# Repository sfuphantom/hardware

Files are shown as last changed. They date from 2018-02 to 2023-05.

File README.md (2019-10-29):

# hardware
Schematics and layout work 

## Getting started with git

Tutorial: https://www.youtube.com/watch?v=1xfp2Cx9FUk

the main workflow is usually like this:

1. install git on your machine https://git-scm.com/download/
2. use the git bash terminal window to work with the repositories:
3. clone the repository of choice: in your terminal window, navigate to the folder you want to store the repository in, and send the command `git clone` https://github.com/sfuphantom/hardware.git' for the hardware repository for example
4. the hardware repo has folders that contain a submodule - which is essentially just a version of a different repo, nested inside the hardware folder. this nested repo is the altium-libraries repository! to enable it, use `git submodule init` while in the hardware directory, and then `git submodule update`
5. now if you navigate to that folder in your normal file browser, you should see the repository folder with all the files in it
6. you can now edit the files and add new files into the repository folder like normal, as you would any folder system
7. to register new added files you have placed in the repository folder in your file browser, use the command `git add -A` in your terminal window while in the directory of your repository (`cd /documents/phantom` will change your active directory to /documents/phantom, and `cd ..` will change your active directory up one level)
8. Make sure you create a new branch before editing any files! Branching instructions down below
9. Once in your new branch, `git add -A` will add all new files repo folder to be tracked by git
10. to save the changes you have made and the files you have added, use the command `git commit -m "fill in your update here"` to commit your changes and save them with a useful message
11. when you are ready to update the centralized repository on github with your changed localized cloned repository, use the command `git push` and you should see your changes show up on github

http://rogerdudler.github.io/git-guide/

https://learngitbranching.js.org/

http://www.ndpsoftware.com/git-cheatsheet.html#loc=workspace

## Branching

If you wish to work on a version of the repo without affecting or potentially causing conflicts, use **branches**. They are very useful for developing a new feature of a program/board without affecting the master branch. They can later be merged into the master branch by using a **pull request**. 
1. Navigate to your hardware directory in the git bash terminal window.
2. Use the following command `git branch MyBranchName` to create a new branch
3. Use the following command `git checkout MyBranchName` to switch your active branch to MyBranchName instead of Master
4. If you want to perform both commands in one line, here's a shortcut: `git checkout -b MyBranchName`
5. Now you can develop and make changes as you wish on MyBranchName, adding files, making commits, and pushing up to the repository held in Github. 
6. When you have decided you are ready to combine your changes/additions to the master branch of the repository, use Github's web interface (https://github.com/sfuphantom/hardware) to create a **new pull request**.
7. A pull request will alert other people that you are ready to combine your branch (MyBranchName) with the Master branch, and will allow them to review your work and approve it for merging.

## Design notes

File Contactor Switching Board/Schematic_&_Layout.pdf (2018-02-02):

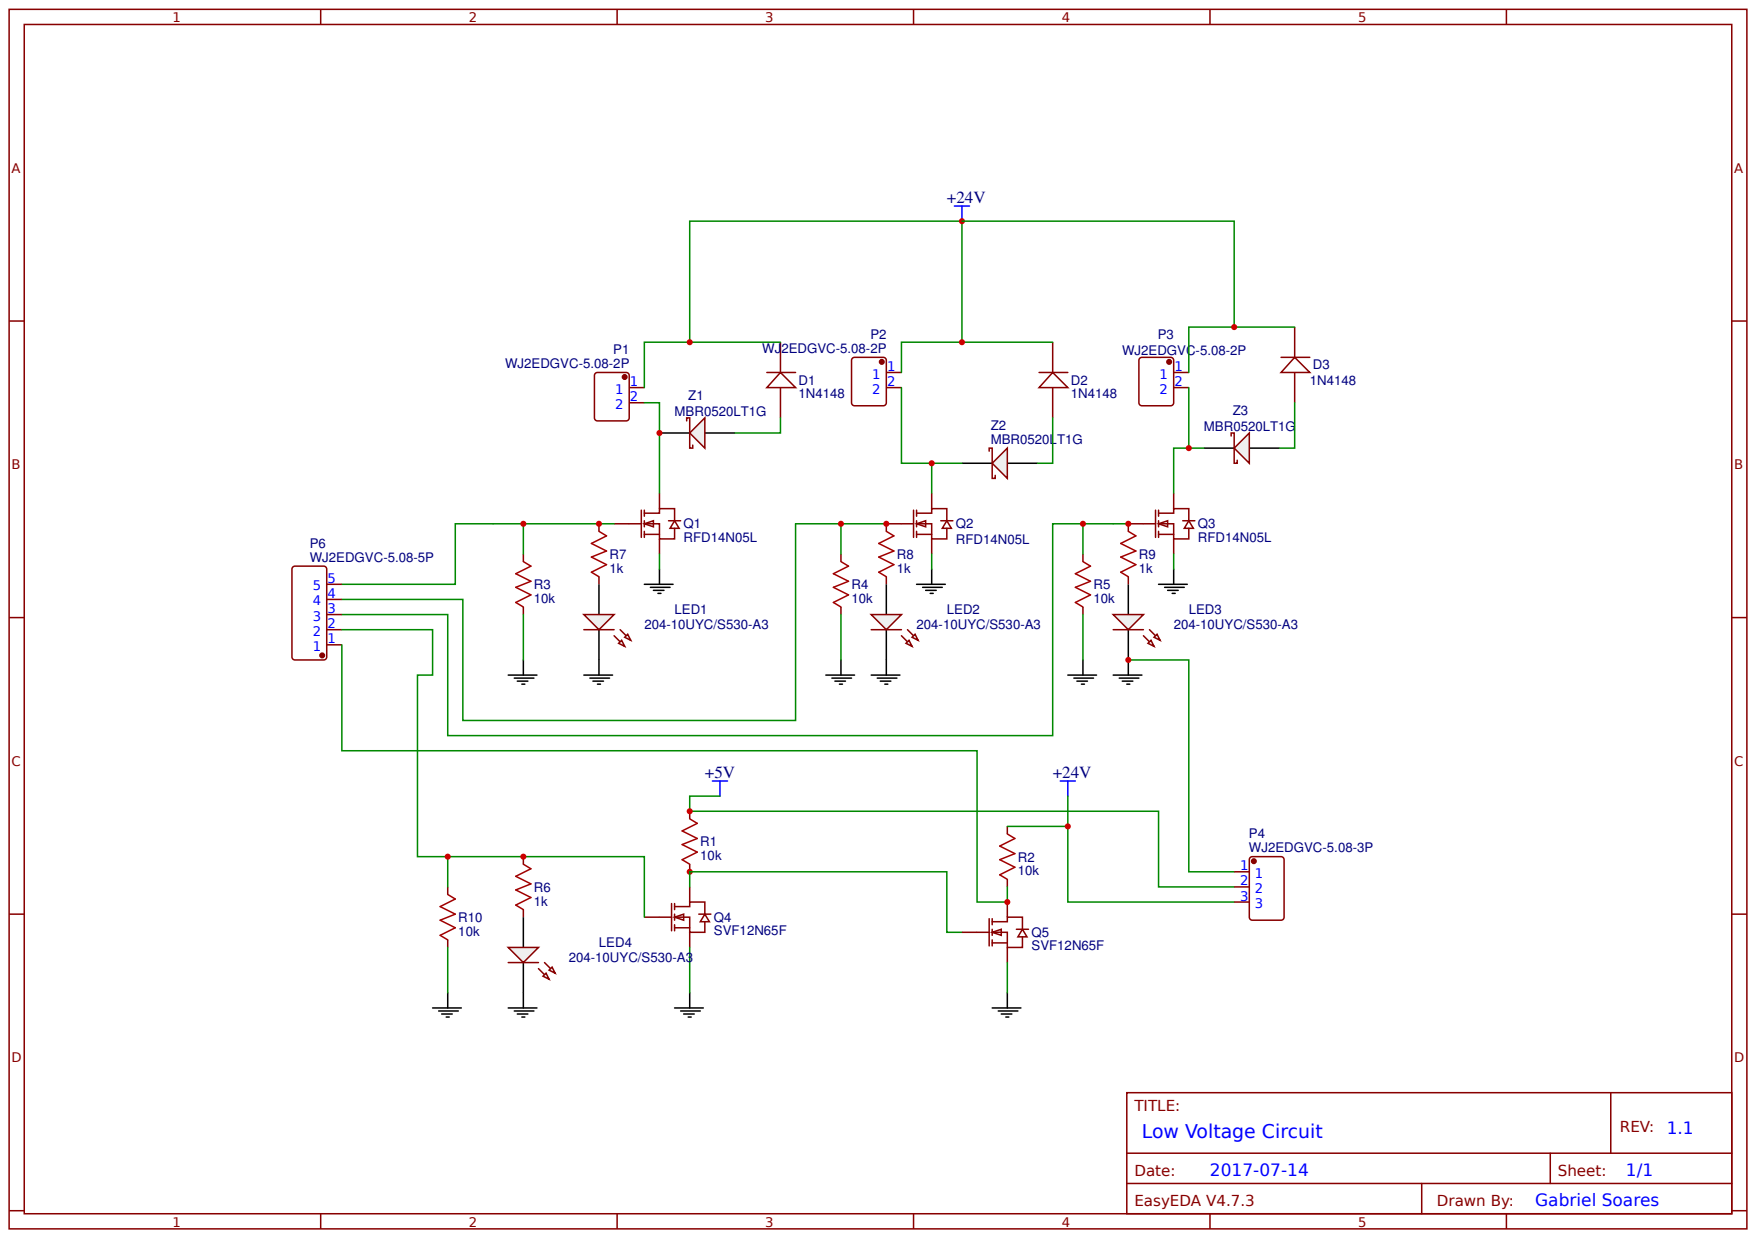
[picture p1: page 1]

Powered by TCPDF (www.tcpdf.org)Powered by TCPDF (www.tcpdf.org)

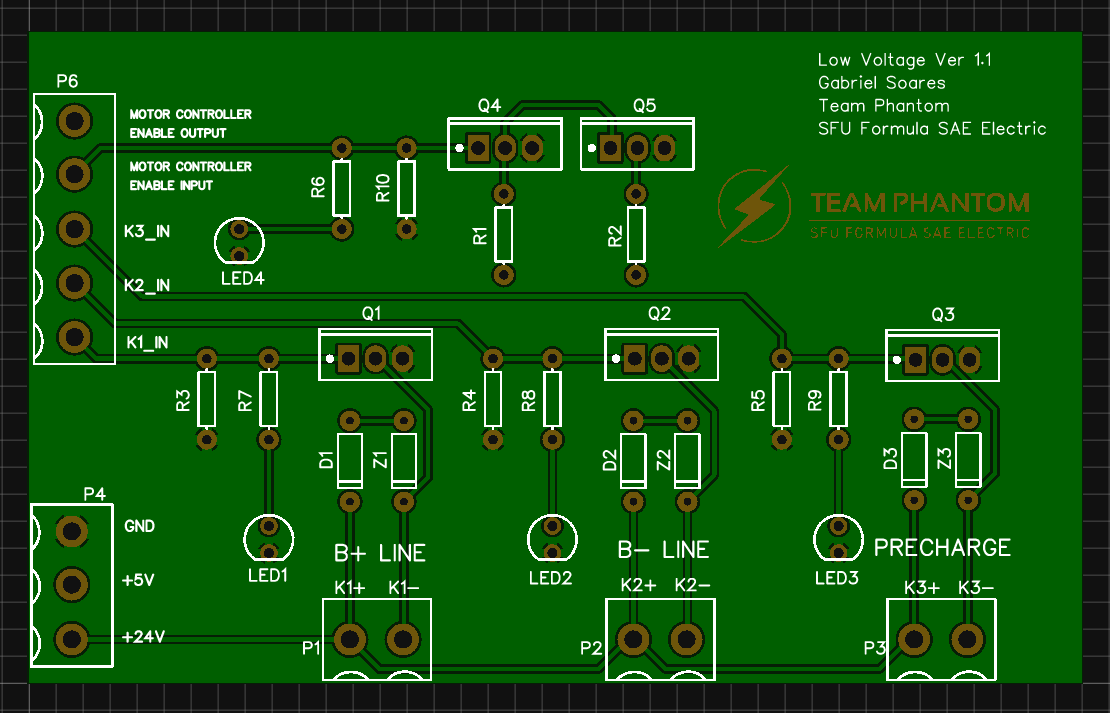
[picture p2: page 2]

Powered by TCPDF (www.tcpdf.org) Powered by TCPDF (www.tcpdf.org) Powered by TCPDF (www.tcpdf.org) Powered by TCPDF (www.tcpdf.org)

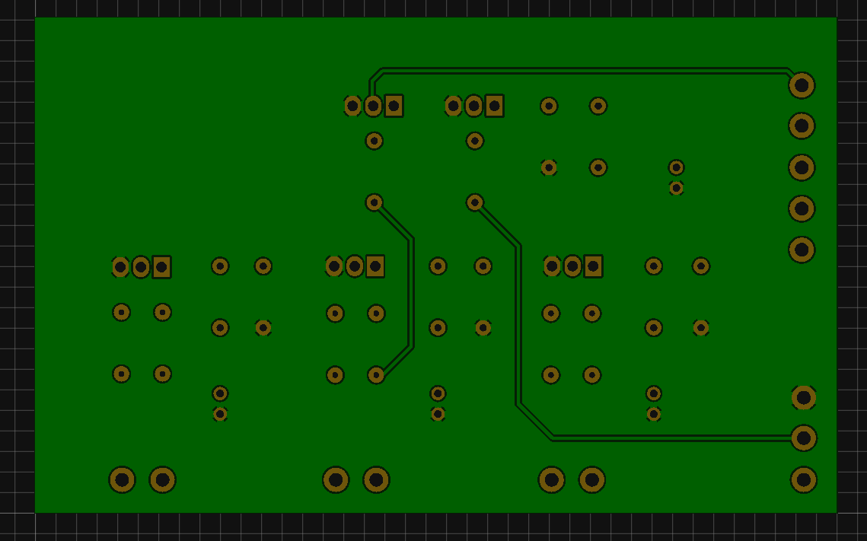
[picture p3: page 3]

Powered by TCPDF (www.tcpdf.org) Powered by TCPDF (www.tcpdf.org)

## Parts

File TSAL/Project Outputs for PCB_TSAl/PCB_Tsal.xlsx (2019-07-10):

Comment | Description | Designator | Footprint | LibRef | Quantity
Fuse |  | F1 | FUSE_SMD | 0678D0800-02 | 1
HV |  | J1 | 2_PIN_CONNECTOR | 0705530001 | 1
LV |  | J2 | 2_PIN_CONNECTOR | 0705530001 | 1
RED LED |  | J3 | 2_PIN_CONNECTOR | 0705530001 | 1
GREEN LED |  | J4 | 2_PIN_CONNECTOR | 0705530001 | 1
NTD2955T4G | Trans MOSFET P-CH 60V 12A 3-Pin(2+Tab) DPAK T/R | Q1 | DPAK228P991X238-3N | NTD2955T4G | 1
IPD50N06S4L-12 | MOSFET N-CH 60V 50A TO252-3-11 | Q2 | DPAK228P998X235-3N | IPD50N06S4L-12 | 1
33k Ohm | RES SMD 33K OHM 5% 1W 2512 | R1 | RESC6332X07N | RMCF2512JT33K0 | 1
1K OHm | RES 1K OHM 1% 1/4W 0805 | R2 | RESC2012X06N | RNCP0805FTD1K00 | 1
190Ohm |  | R3 | RESC2012X06N | RC0805FR-0719R1L | 1
560 Ohm | RES SMD 560 OHM 5% 0.4W 0805 | R4 | RESC2012X06N | ESR10EZPJ561 | 1
EL3H7(B)(TA)-VG | OPTOISOLATOR 3.75KV TRANS 4-SSOP | U1 | SOIC127P700X200-4N | EL3H7(B)(TA)-VG | 1

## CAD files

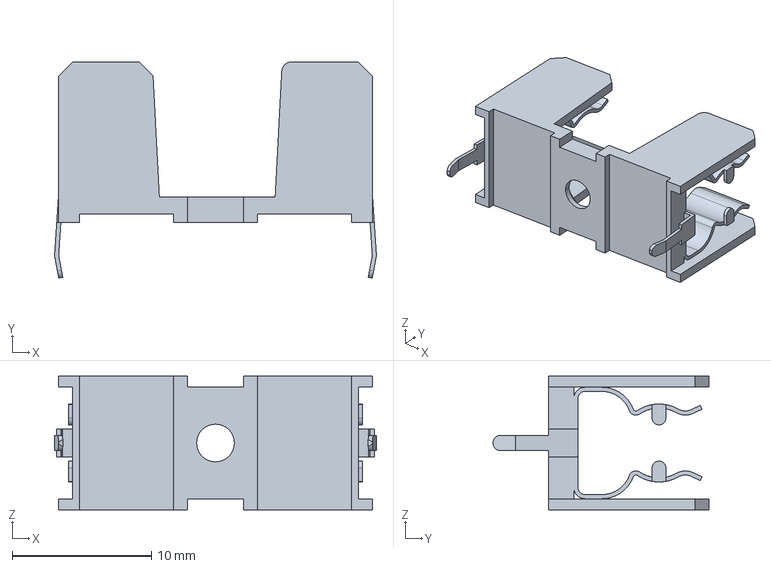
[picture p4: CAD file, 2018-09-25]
PDB/step_files/fuse.stp
23.1 x 15.5 x 9.60 mm

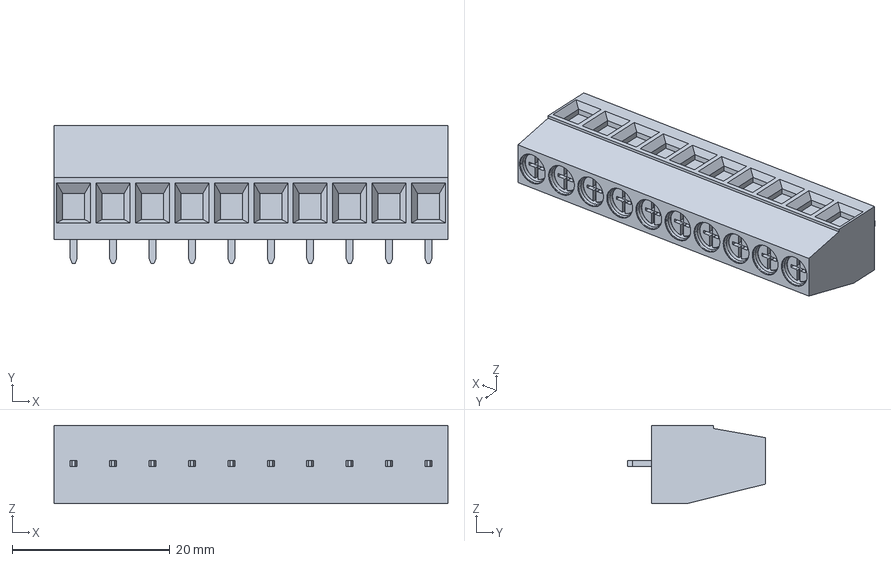
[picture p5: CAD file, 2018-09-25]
PDB/step_files/hdr2.stp
50.0 x 17.5 x 9.91 mm

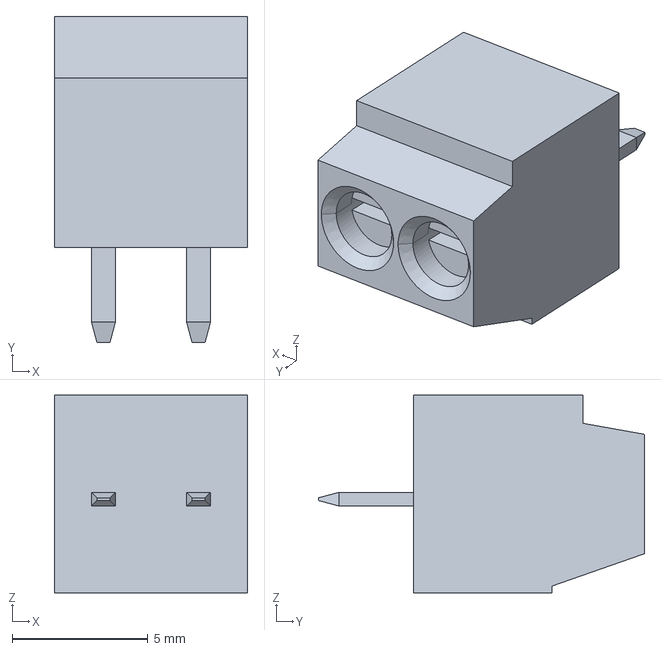
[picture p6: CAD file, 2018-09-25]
PDB/step_files/hdr1.stp
7.11 x 12.0 x 7.29 mm

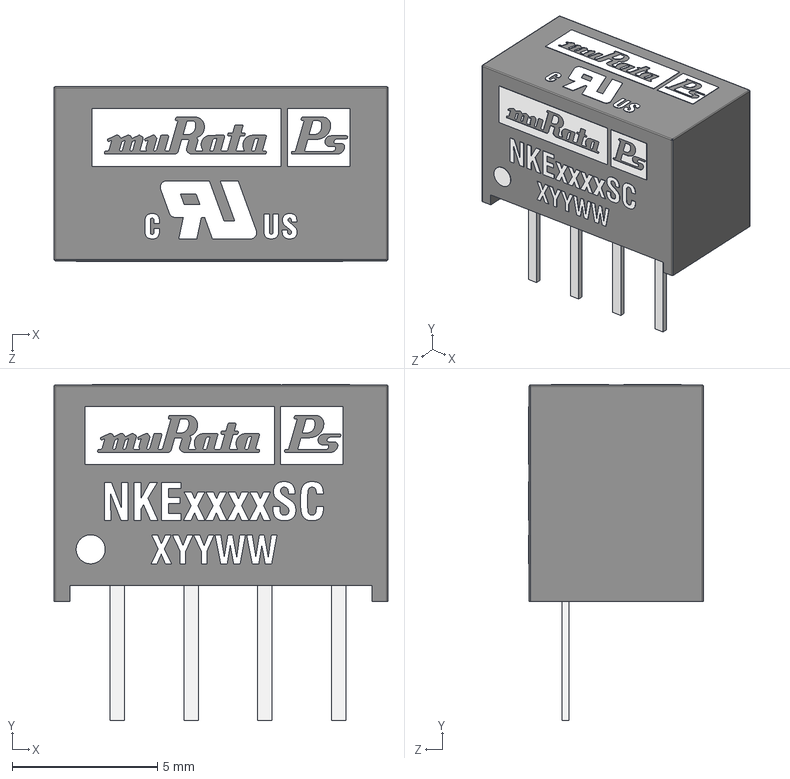
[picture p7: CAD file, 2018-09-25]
PDB/step_files/dcdc2.step
11.5 x 11.6 x 6.02 mm

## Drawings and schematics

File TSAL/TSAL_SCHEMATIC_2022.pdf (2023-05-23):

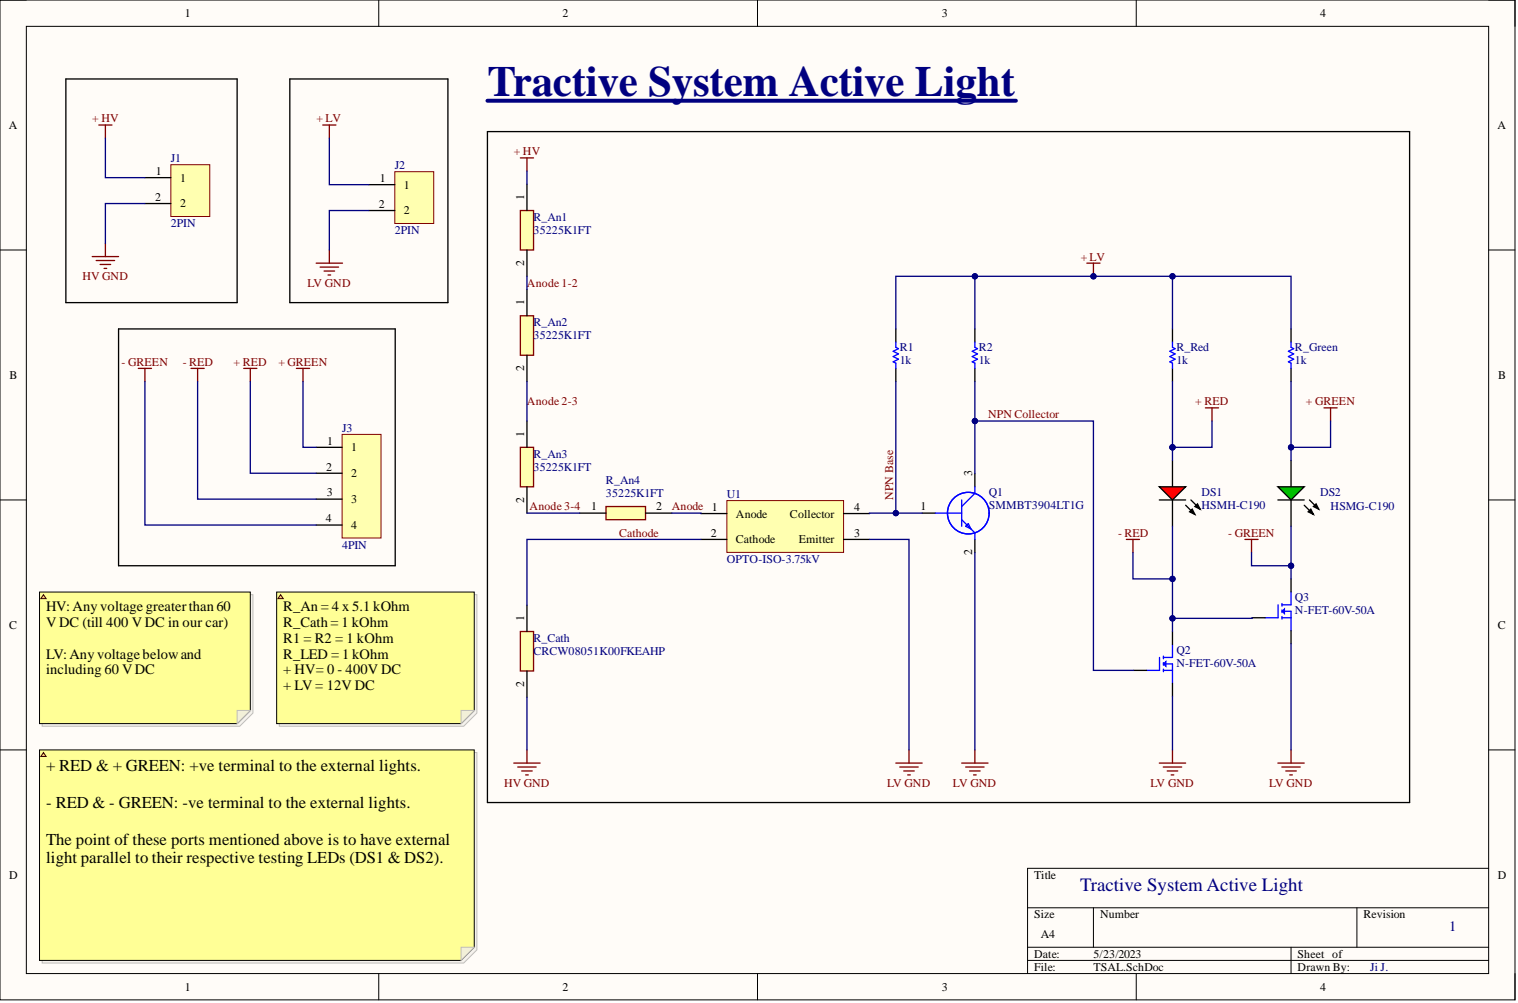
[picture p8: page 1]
1 2 R_Cat; NPN Base; NPN Co; ater th; V DC (till; + RED; the external; - RED; these ports; ioned above; ight paral; their respect; ing LEDs (DS1

Tractive System Active Light

The point of

to have external

Tractive System Active Lig

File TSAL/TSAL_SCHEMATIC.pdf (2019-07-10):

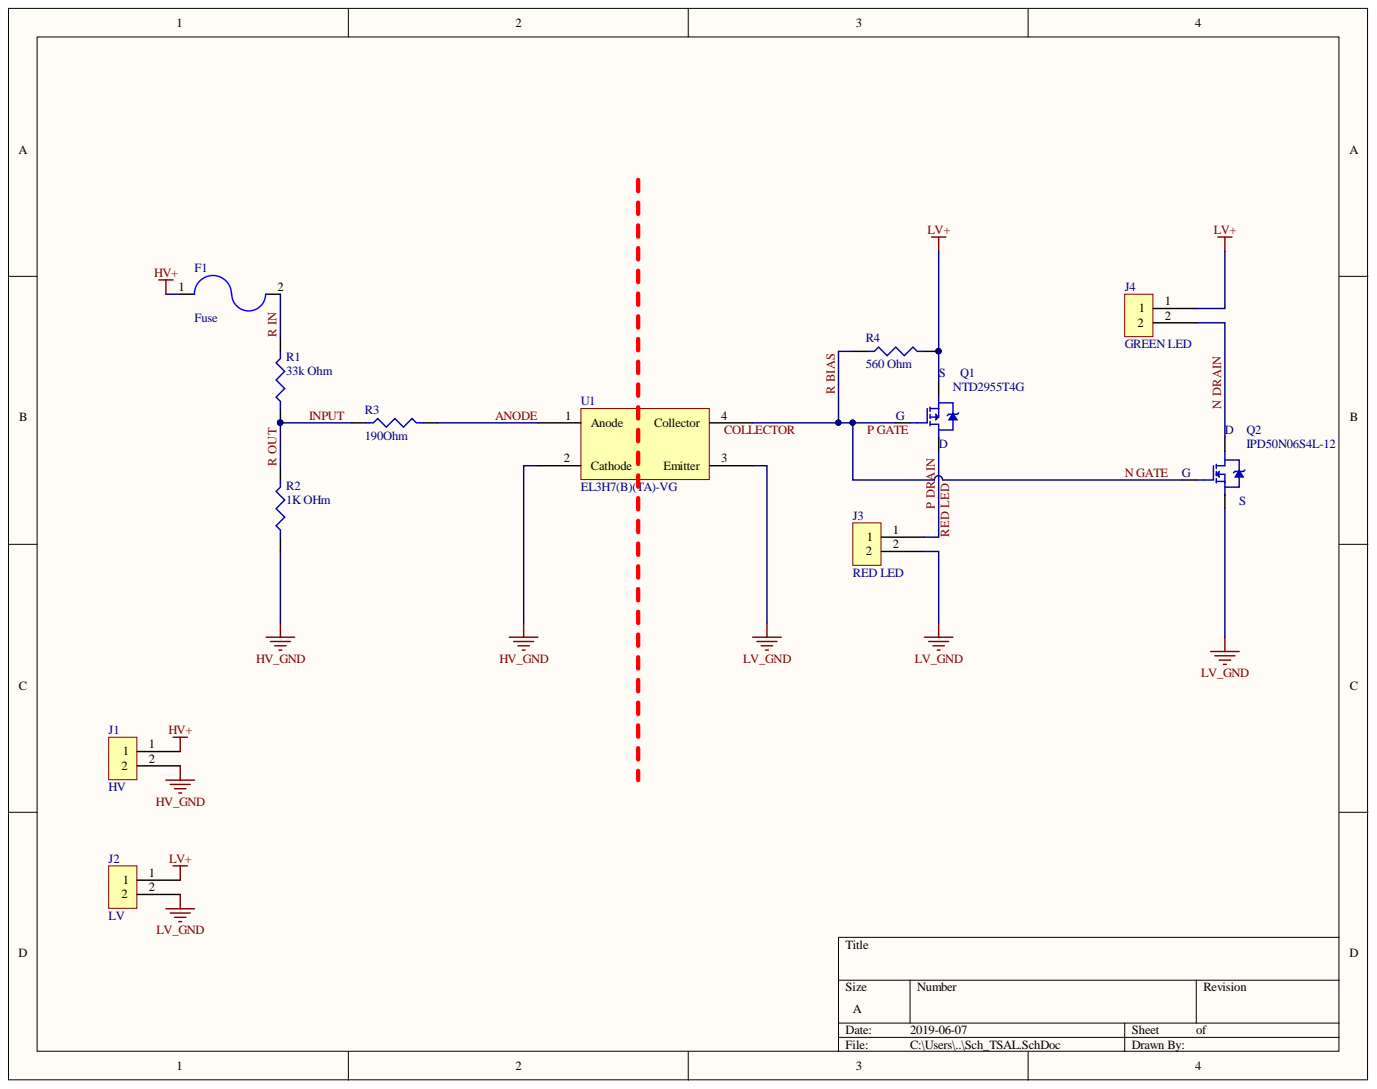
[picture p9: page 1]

Anode 1

COLLECTOR

Size A | Number | Revision

Date: 2019-06-07 | Sheet of
File: C:\Users\..\Sch_TSAL.SchDoc | Drawn By:

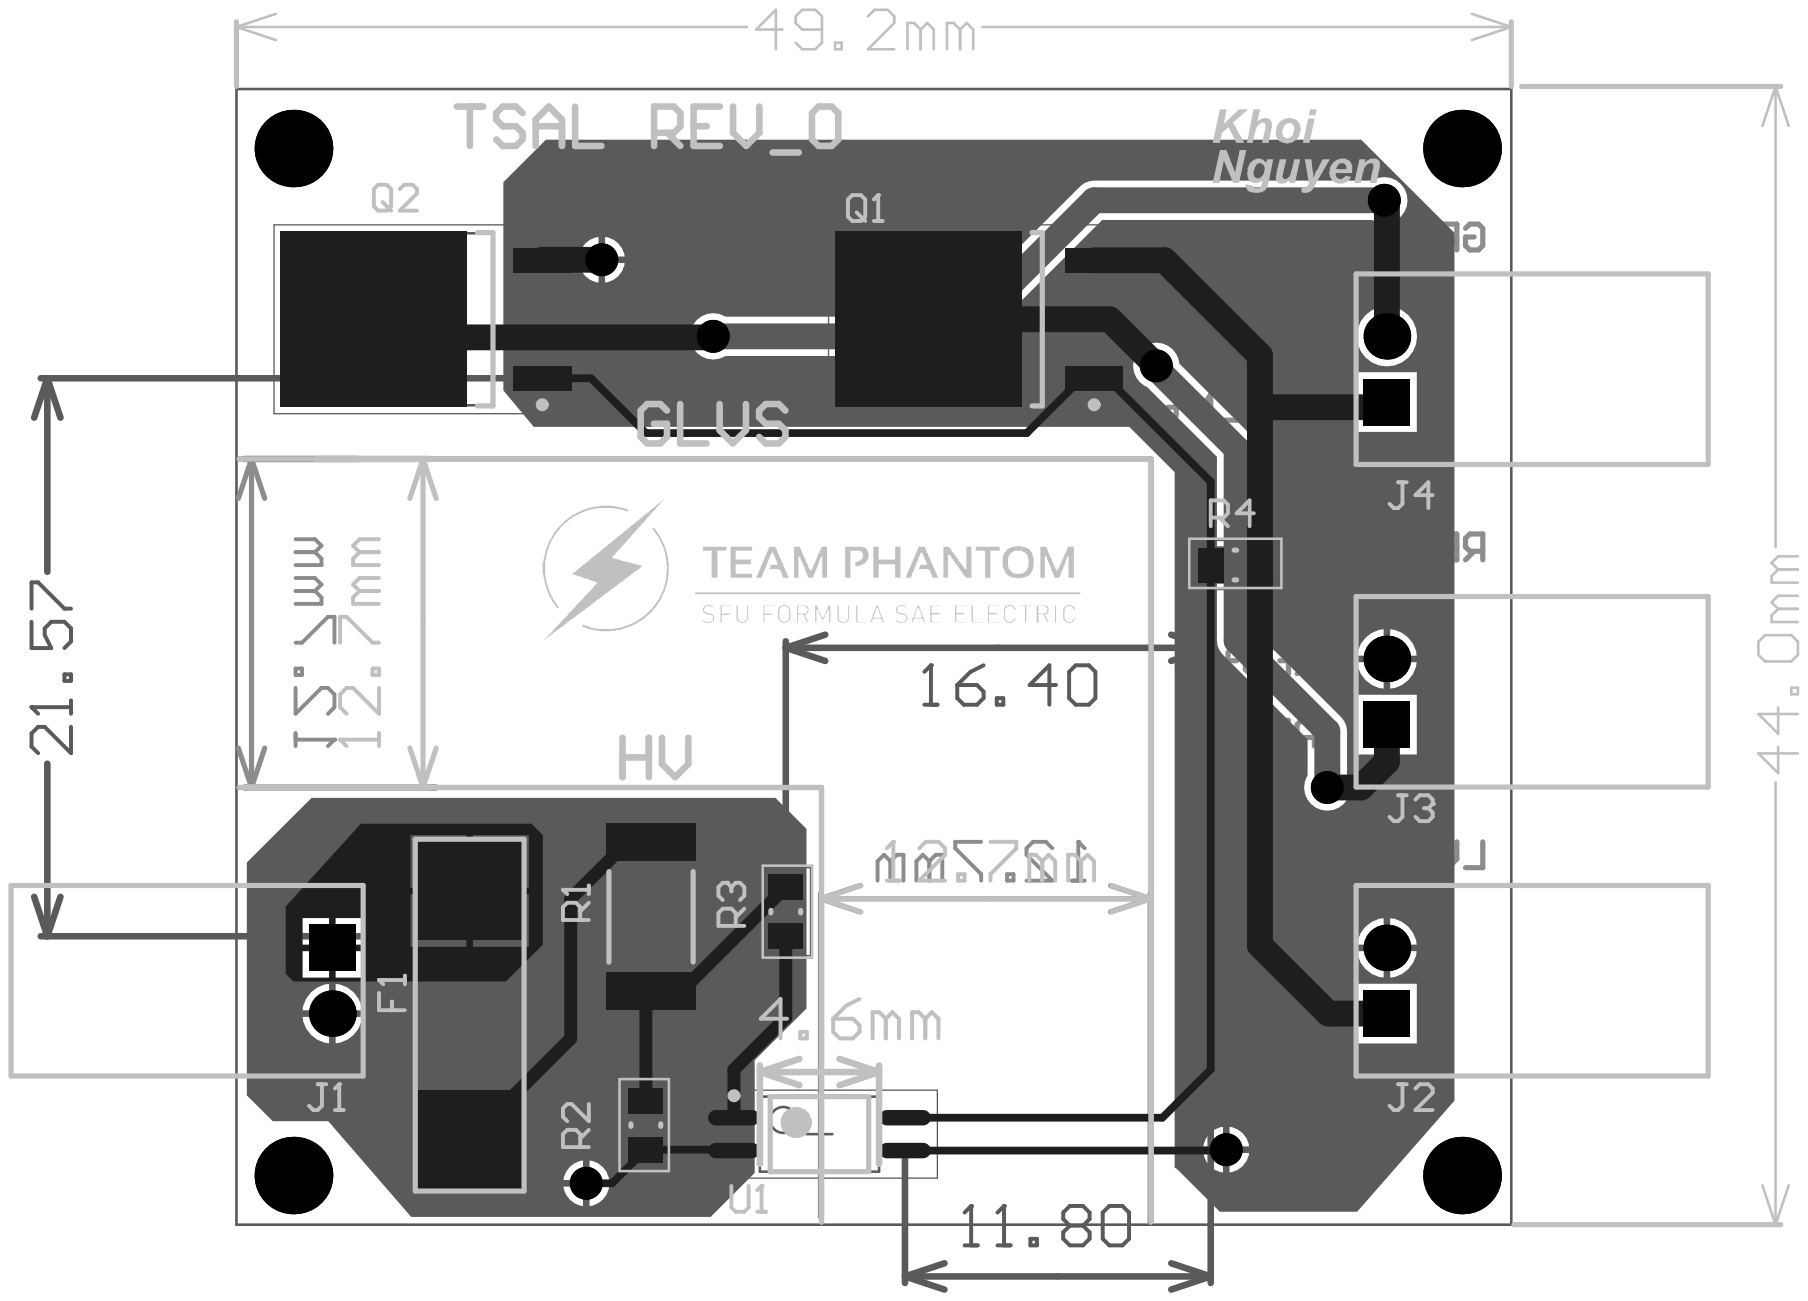
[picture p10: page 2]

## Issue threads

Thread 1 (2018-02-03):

24V Input Connector

gabesoares, 2018-02-03:
Need to find 24V input connector for power input to VCU

gabesoares, 2018-02-07:
Will use Molex MegaFit Connectors:
https://www.molex.com/molex/products/family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

Up to 23.0A current capability
12 - 16 AWG

Board Connector: https://www.digikey.com/products/en?keywords=0768250002

Wire Crimp Connector: https://www.digikey.com/products/en?keywords=1700010102

Crimp Sockets: 12 AWG - https://www.digikey.com/product-detail/en/molex-llc/0768230322/WM11982CT-ND/5639626
14 & 16 AWG - https://www.digikey.com/product-detail/en/molex-llc/0768230321/WM11981CT-ND/5639625

Closed 2018-02-07.

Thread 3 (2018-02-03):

Error Reset Push Buttons

gabesoares, 2018-02-03:
Add push buttons for nPORRST and nRST as inputs to the TMS570 mcu

gabesoares, 2018-02-08:
Added, soft reset and hard reset

Closed 2018-02-08.

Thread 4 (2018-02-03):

Higher Current DCDC

gabesoares, 2018-02-03:
Should we replace the 2A 24->5V DCDC with a higher current one?  Additional current draw from new components plus inrush on the AIRs will likely exceed the rating of our current DCDC, which would result in the voltage rail dropping

gabesoares, 2018-03-19:
Yes

Closed 2018-03-19.

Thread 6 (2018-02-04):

Prototype Latching Circuit

gabesoares, 2018-02-04:
Order components and prototype JK flip flop latching circuit
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

gabesoares, 2018-02-04:
Desired operation: fault signal is sending 0 as all is good, then a fault occurs and the signal sends a 1 (+5V) for a second and then drops back to 0.. We want this 1 to stay latched forever...

JK Flip Flop Logic:
If J=0, K=0, then output Q (& Q bar) stays latched to whatever it was before
If J=1, K=0, then output Q is set to 1, and Q bar is set to 0
If J=0, K=1, then output Q is set to 0, and Q bar is set to 1
If J=1, K=1, then output Q and Qbar are both toggled to the opposite of what they were before

NOTE: A clock signal is needed for the JK flip flop, a 555 timer can be used to generate the clock, but the exact circuit will need to be looked up

The push button attached to the K input will allow the output Q to be reset to 0, and Q bar to be reset to 1.
The red error LED should light up if the fault signal sends a 1 and the output is latched, and turn off when the push button (reset) attached to the K input is pressed.

The green LED should be on in normal operation, and as soon as the fault signal sends a 1. It should stay off until the reset push button is pressed. (This green LED simulates the relay coils of the AIRs)

gabesoares, 2018-02-08:
Prototype this latching circuit as well, talk to Will to learn more about it:

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

Will-McKnight-604, 2018-02-14:
Updated Latching Circuit

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

gabesoares, 2018-02-14:
Latest latching circuit
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

gabesoares, 2018-02-14:
Will need high side driver instead of FET, since vgs will be tough to get without a charge pump, especially with a microcontroller output:

This one looks good, Rds(ON) a little high but not really significant for low current and turning on a relay, it also has a lower pin count and less external components than the other automotive TI ones
http://www.ti.com/product/tps1h000-q1

Will-McKnight-604, 2018-02-20:
Hanieh is taking the flip-flop circuit and prototyping that one, I'll be doing the latest latching circuit

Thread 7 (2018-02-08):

Prototype Shutdown Circuit

gabesoares, 2018-02-08:
Prototype first version of shutdown circuit. Wire inline buttons to simulate the inertia switch, brake over travel switch, HVD, and other master switches.

Use mosfets as shown in attached picture, you might need to be careful about the Vgs of each fet.
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

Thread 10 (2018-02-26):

Find better 1V2 zener diode

gabesoares, 2018-02-26:
3.3V reverse breakdown might be too high.. will likely need new footprint

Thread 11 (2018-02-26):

Change via sizes to bigger holes

gabesoares, 2018-02-26:
Current holes result in min hole size being changed to 0.2 from fab house

gabesoares, 2018-06-09:
Changing from 0.4mm to 0.6mm seems to work

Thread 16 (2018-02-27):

Find smaller crystal

gabesoares, 2018-02-27:
Current one too big, good price though ($0.46 usd)

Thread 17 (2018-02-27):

Find new MCU

gabesoares, 2018-02-27:
Stay within tms570 family, find one with smaller packaging since we don't use all the pins anyway, and one that can be sampled from TI

gabesoares, 2018-10-24:
Figure out how different the TMS570LS1227PGEQ1 is from our TMS570LS1224PGEQ1.... since this one we can potentially sample from TI. Might be worth a few changes to switch to this one. Looks like most of the same features are there, need to verify pinout.
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

gabesoares, 2018-10-30:
Almost identical, but x1227 has FlexRay in addition so has a few less GPIOs than the x1224. Other than these the pinout is identical. Managed to get 3 ICs sampled which is good. Need to be careful tho cause if can't get more sampled, they cost $37 each from Digikey...

http://www.ti.com/lit/ds/symlink/tms570ls1227.pdf

gabesoares, 2019-04-18:
Done, validated TMS570LS1227 on REV1 of VCU

Closed 2019-04-18.

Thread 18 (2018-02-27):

Change routing from D15

gabesoares, 2018-02-27:
Trace on ground side of zener should be on bottom layer

gabesoares, 2018-12-30:
Fixed in vcu-hw rev1

Closed 2018-12-30.

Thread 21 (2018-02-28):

Add voltage sensing on all the rails

gabesoares, 2018-02-28:
Using op amps to compare voltage rails to ensure they are operating nominally. Currently even if a rail is half up (i.e. 24V rail is running at 12V for some reason), our power good LED will still turn on

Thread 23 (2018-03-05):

Create footprint for combined conector

gabesoares, 2018-03-05:
The two molex stac64 connectors need a combined footprint with the mounting holes 4.96mm apart, with both 3d models in one part.

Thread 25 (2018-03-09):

Switch to cheaper FETs

gabesoares, 2018-03-09:
Use lower rated FETs on VCU, current ones are overkill and can handle way too much (i.e. 110 amps). They are expensive, too big, and also hard to solder

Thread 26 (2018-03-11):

Add pull down resistors to ADC input

gabesoares, 2018-03-11:
Without pulldowns they will float, i.e. if a wire disconnects by accident the signal won't be zero

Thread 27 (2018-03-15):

Add EEPROM for parameter saving

gabesoares, 2018-03-15:
Add EEPROM IC to VCU, is useful to dump parameters and values periodically in case of an unexpected loss of power. Upon reset of MCU data can be loaded back with a timestamp of the last data dump

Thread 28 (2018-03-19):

Higher Current DCDCs

gabesoares, 2018-03-19:
Find higher current DCDCs for 3V3 and 5V rails, current ones blow really easily (5V one at 2A and 3V3 one at 300mA). Also find ones that have a much smaller footprint to save board space

gabesoares, 2019-04-18:
Switched to 5A buck https://www.digikey.ca/product-detail/en/diodes-incorporated/AP65550FN-7/AP65550FN-7DICT-ND/5147405

Closed 2019-04-18.

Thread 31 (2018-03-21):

Add info to PCB doc

gabesoares, 2018-03-21:
Create better fab layer, show stackup, copper thickness, trace min width, impedance, min hole size. Add keepins and keepouts, and use only one mechanical layer for components instead of two

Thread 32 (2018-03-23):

Increase low side driver trace width

gabesoares, 2018-03-23:
Increase trace width through drain-source path of low side drivers for contactor switching. Want a low resistance/inductance path for contactor relay coil current pass through, without getting hot. The increased thickness will also help heatsink the FETs. Consider making them small planes.

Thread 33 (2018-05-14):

Fix 24V->5V DCDC footprint

gabesoares, 2018-05-14:
Current one has 24V and 5V mixed up.. leading to the DCDC having 24V put to its output... This is fixed on the board by placing the DCDC upside down on the PCB

gabesoares, 2019-04-18:
Fixed but also decided to no longer use this DCDC.

Closed 2019-04-18.

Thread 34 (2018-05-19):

Change LDO to 1V2

gabesoares, 2018-05-19:
Current one is rated for 3.3V output... which means when it has a 3.3V input it outputs around 2.3V. Buy the 1V2 one.

https://www.digikey.ca/product-detail/en/texas-instruments/LP5912-1.2DRVT/296-46645-1-ND/7219079

gabesoares, 2019-04-18:
Fixed, switched to MIC5504 which can do 300mA, might still be too low a current when the 570 is running fully, need to test. https://www.digikey.ca/products/en?keywords=576-4878-1-ND

Closed 2019-04-18.

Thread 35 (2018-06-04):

JTAG Power

gabesoares, 2018-06-04:
Look into providing power through JTAG instead of needing a separate usb connector.

gabesoares, 2018-07-18:
In code composer, select the target configuration (.ccxml file). Click on the 'advanced' tab at the bottom of the screen. Then click on the XDS110 debugger in the left browsing window, on the right a drop-down menu allows the selection of probe-supplied power. This is supposedly where the debugger would be able to supply 3V3... still need to check it. By default it is on target-supplied power

gabesoares, 2018-07-20:
Looks like power is supplied through the auxiliary connector, which the VCU doesn't have an input for. Will need external power to be supplied

Closed 2018-07-20.

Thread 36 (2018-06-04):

Find Fast Blow Fuses

gabesoares, 2018-06-04:
Current fuses on 5V, 3V3, and 1V2 rails on VCU do not blow at their rated currents. Check in datasheet to find trip curve, and find fuses that are fast blow and will trip when needed.

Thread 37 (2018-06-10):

MCU Debugger Additions

gabesoares, 2018-06-10:
Add more debuggers to our inventory to support embedded team. We currently only have 1 CCS 110  debugger, look into adding J-Link Seggers as well.

See list of supported debuggers for our MCU here under 'emulators' :

http://www.ti.com/microcontrollers/hercules-safety-mcus/tools-software.html

gabesoares, 2018-06-11:
XDS 110 debug probe guide:

http://www.ti.com/lit/ug/sprui94/sprui94.pdf

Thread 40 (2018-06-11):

Derate all ceramic and tantalum capacitors

gabesoares, 2018-06-11:
Make sure all MLCC and tantalum polymer capacitors on the VCU are properly derated. They've just been selected based on rated capacitance and voltage.

MLCC: Multi Layer Ceramic Capacitor

Reference these derating guidelines, find some also for MLCC:
https://www.digikey.com/en/ptm/k/kemet/derating-guidelines-for-surface-mount-tantalum-capacitors

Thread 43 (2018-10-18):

Schematic Design

gabesoares, 2018-10-18:
Design schematic on paper for TSAL, red LED blinking for HV and green solid LED for LV.

gabesoares, 2018-10-21:
High level block diagram from @Khoideptrai123 :
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

gabesoares, 2019-04-18:
@Khoideptrai123 is the schematic in altium finalized? If so please comment with the commit hash in which it was finished.

Khoideptrai123, 2019-04-19:
[TSAL Circuit-1.pdf.pdf](https://github.com/sfuphantom/hardware/files/3099386/TSAL.Circuit-1.pdf.pdf)
This is the final schematic

gabesoares, 2019-04-20:
Latest version of schematic almost done, here df24efb

Closed 2019-04-20.

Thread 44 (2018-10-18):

Bill of Materials

gabesoares, 2018-10-18:
Finalize all parts needed for TSAL circuit

gabesoares, 2019-04-18:
@Khoideptrai123 @sumreenr is this finalized? If so please comment saying so and close the issue

Khoideptrai123, 2019-04-19:
The BOM is finished!

https://docs.google.com/spreadsheets/d/1D_N_h-VSUfupYI5B_tzBBqGqgnA3iFfgFhU_PEmYJnU/edit#gid=0

Closed 2019-04-19.

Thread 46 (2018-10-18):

5V, 3V3, & 1V2 rails down

gabesoares, 2018-10-18:
Fix the broken power rails on the VCU. Something looks like it is wrong with the 5V OR-ing controller as it is burning hot when on. Board now draws 140mA from power supply with 5V, 3V3, and 1V2 rails down. Previously drew 60-80mA under normal operation.

gabesoares, 2018-10-19:
Seem to be related to CAN transceivers... both seemed to be drawing too much current on 5V rail. This is the second time the CAN transceiver has been the culprit for a 5V rail drop.

Double check schematic connections and IC.

gabesoares, 2018-10-21:
Looks like the schematic connection is wrong, connected VSS to 5V and VDD to GND. Should be the other way around.. This explains why whenever the CAN transceivers are soldered the 5V rail gets messed up. Need to rework the board by cutting some traces and jumping them to switch VSS and VDD.
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

gabesoares, 2018-12-28:
Fixed in rev1, in vcu-hw repo commit 7288ddc6

Closed 2018-10-21.

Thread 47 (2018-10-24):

Create XDS110 adapter

gabesoares, 2018-10-24:
Need adapters for 20-pin TI JTAG interface to 10-pin ARM connection for JTAG that is on the VCU. Can be a good starter PCB project for new members.

gabesoares, 2018-10-24:
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

gabesoares, 2019-04-18:
Fixed by @neeerajb in 3a6f558

Closed 2019-04-18.

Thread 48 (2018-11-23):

BSPD

raajc, 2018-11-23:
Notes November 22, 2018
Faraz and Raaj

Last time we tested the comparator and the inverter. The Inverter worked as expected, the comparator had open drain output (active low), not the same problem on PCB, and required a pull-up resistor on the outputs.

raajc, 2018-11-23:
AND gate works as expected!

Closed 2018-11-23.

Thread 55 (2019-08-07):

Question: How effective is the TSAL?

michaelruppe, 2019-08-07:
Hey friends,
I'm working on my own comparator-based TSAL, but your solution is attractive owing to it's simplicity. If you have the time spare, I have a couple of questions:

- Does it trigger at a repeatable and accurate voltage? (both the turn-on and turn-off)
- Does the circuit need tuning? I imagine that for the small currents at the optocoupler LED, small manufacturing differences between optocouplers of the same type could change the trigger levels substantially. What have you experienced?
- How's the power dissipation in the input voltage-divider?
- What voltage accumulator are you running?

I appreciate any time you take to answer these questions - I know well how short time is when building a race car.
If you prefer to answer outside of the public domain you can reach me at:
michael.ruppe@live.com.au

Thanks, and best of luck.

Khoideptrai123, 2019-08-14:
Hi Micheal,
My name is Khoi from Team Phantom FSAE.  We are still testing the TSAL right now, so the result is incomplete!
For your question, I have a couple of answers:
- The TSAL works in the range of 92V and above. We start testing the HV below 92V and the optocoupler does not work in accordance with its behaviors. However, our HV system runs from 120V to 168V so we have enough margin to maintain the behaviors of the optocoupler.
-For us, we use 168V for the voltage accumulator, so for the divider, we just pick the resistors that could maintain the power ( as P = V^2/R ) so the power dissipation is around 0.83W which is okay for our PCB.

I hope this answers your question. Please feel free to contact us if you have any questions.
Thank you and wish you the best, Micheal

Khoi,
Electrical member of Team Phantom

michaelruppe, 2019-09-03:
I appreciate the response, Khoi :thumbsup:
In the end I stuck with my [comparator-based design](https://github.com/michaelruppe/FSAE/tree/master/TSAL) to keep the switching threshold as close as possible to the 60V (Australian competition).

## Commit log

2018-02-02 Added LV Contactor Board Fab Outputs
    [LV+Schematic.schdoc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]
2018-02-02 Added altium files & pdf of schematic & layout
    [Contactor_Switching.pcbdoc]
2018-02-03 Added VCU project
    [ADC_Decoupling.SchDoc, CAN.SchDoc, Connectors.SchDoc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]
2018-02-03 file cleanup
    [ADC_Decoupling.SchDoc, CAN.SchDoc, Connectors.SchDoc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]
2018-02-03 fixed submodule
    [ADC_Decoupling.SchDoc, CAN.SchDoc, Connectors.SchDoc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]
2018-02-03 placed decoupling caps on VCU tms570
    [PHANTOM_VCU.PrjPcb, Power_MCU.SchDoc, VCU_Schematic.SchDoc]
2018-02-07 Updated libraries in hardware folder
    [Connectors.SchDoc, MCU_Signals.SchDoc, PHANTOM_VCU.PrjPcb]
2018-02-07 Placed 1V2 LDO on vcu, placed jtag connector with resistors
    [Connectors.SchDoc, MCU_Signals.SchDoc]
2018-02-08 major layout changes in vcu
    changed board size, re-placed components, added reset buttons, rail test points
    [ADC_Decoupling.SchDoc, CAN.SchDoc, Connectors.SchDoc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]
2018-02-14 power routed to tms570, 1v2 and 3v3 on vcu
2018-02-14 placed usb connector
    [MCU_Signals.SchDoc, VCU_Schematic.SchDoc]
2018-02-15 added ftdi chip, ferrite beads, decoupling caps, usb diff pair routing needs work, placed jtag, routed first half, routed uart, routed foot pedal analog signals
    [Connectors.SchDoc, MCU_Signals.SchDoc, VCU_Schematic.SchDoc]
2018-02-16 Added 8 position connector to vcu
    4 pins power, 4 pins ground
    [Connectors.SchDoc]
2018-02-17 started on overall car electrical schematics
    [High Level.SchDoc, Overall_Schematics.PrjPcb]
2018-02-17 added APPS
    [BlockDiagramParts.SchLib, High Level.SchDoc, Overall_Schematics.PrjPcb]
2018-02-17 switched spi buses between dac and gpio expander
    [VCU_Schematic.SchDoc]
2018-02-18 routed 5v from bat and from usb through switching mux
    [Connectors.SchDoc, MCU_Signals.SchDoc, Power_Sensing.SchDoc]
2018-02-18 cleaned up bottom layer routing, starting on contactor enable lines
    [Connectors.SchDoc]
2018-02-19 routed contactor switching in vcu
2018-02-19 routed i2c lines in vcu
2018-07-18 added new project
    [555.PrjPCB]
2018-09-25 LV PDB scematic and pcb design
    footprints and values need to be changed
    [PCB.REV6.PcbDoc, PDB.rev1.SchDoc, dcdc2.step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]
2018-11-22 Hello 555 my old friend
    [555_khoi.PrjPCB, FOOT_PRINT_K.PcbLib, SCH_LIB.SchLib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]
2018-11-22 added schematic symbol
    [Schematic_library.SchLib]
2018-11-23 Hi mom I'm adding 1kohm resistor to the library
    [FOOT_PRINT_K.PcbLib, PCB_Project1.PrjPCB, PcbLib1.PcbLib]
2018-11-23 New TSAL branch
    [PCB_Project2.PrjPCB, SCH_LIB.SchLib, Schlib1_Nmos.SchLib]
2018-11-24 Added footprint for N channel mosfet
    [Footprint_Nmos.PcbLib, PCB_TSAl.PrjPCB, Schlib1_Nmos.SchLib]
2018-11-25 Added shchematic for photocoupler
    [PCB_TSAl.PrjPCB, Schlib1_Nmos.SchLib, Schlib1_TSAL.SchLib]
2018-12-17 rename the schematic lbrary name and PCB library
    [FOOT_PRINT_K.PcbLib, Footprint_Nmos.PcbLib, SCH_LIB.SchLib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]
2018-12-18 Fix the schematic for N mosfet
    [FOOT_PRINT_K.PcbLib, SCH_LIB.SchLib, Schlib1_TSAL.SchLib]
2019-03-15 Deleting old schematic and adding new components to schematic library
    [Schlib1_TSAL.SchLib]
2019-03-16 Adding resistor, optoisolator, mosfet
    [Footprint_Nmos.PcbLib, Schlib1_TSAL.SchLib]
2019-03-16 Adding footprint for 2 mosfet
    [Footprint_Nmos.PcbLib, Schlib1_TSAL.SchLib]
2019-03-22 Adding the temporary schematic
    [Sch_TSAL.SchDoc, Schlib1_TSAL.SchLib]
2019-04-19 Adding connector footprint + update schematic
    [Footprint_Nmos.PcbLib, PCB_TSAl.PrjPCB, Sch_TSAL.SchDoc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]
2019-04-20 Updating footprint + schematic + PCB
    [Footprint_Nmos.PcbLib, PCB_TSAl.PrjPCB, PCB_Tsal.PcbDoc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]
2019-04-25 Updating libraries+ schematic+ PCB
    [Footprint_Nmos.PcbLib, PCB_Tsal.PcbDoc, Sch_TSAL.SchDoc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]
2019-05-02 Adding silkscreen and replacing components of the PCB for TSAL
    [PCB_Tsal.PcbDoc, Sch_TSAL.SchDoc]
2019-05-15 Adding fuse and updating the schematic
    [Footprint_Nmos.PcbLib, PCB_Tsal.PcbDoc, Sch_TSAL.SchDoc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]
2019-05-19 Updating routing and powerplane
    [Footprint_Nmos.PcbLib, PCB_Tsal.PcbDoc, Sch_TSAL.SchDoc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]
2019-05-24 Updating schematic +PCB
    [PCB_Tsal.PcbDoc, Sch_TSAL.SchDoc]
2019-05-31 Q1 source and drain pins were flipped
    [Footprint_Nmos.PcbLib, PCB_Tsal.PcbDoc, Sch_TSAL.SchDoc]
2019-06-07 Added silk on bottom side, widened LED current traces, added board outline and generated gerber+drill files
    [PCB_Project2.PrjPCB, PCB_TSAl.PrjPCB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]
2019-07-08 Include the BOm and delete unnecessary file
    [555.PrjPCB, 555_khoi.PrjPCB, FOOT_PRINT_K.PcbLib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]
